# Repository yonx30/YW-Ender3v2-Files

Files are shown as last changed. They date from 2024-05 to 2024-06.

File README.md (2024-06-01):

# YW's Ender 3v2 Files
Repo for my custom files for the Ender 3v2 Enclosure and Jyers firmware.

## Modified Ender 3v2 



### Lack Enclosure
Printable parts to construct a standard I3 style 3D printer enclosure using 2x Ikea Lacks

Lack enclosure remixed based on the Ender 3 V2 Ikea Lack 3D Printer Enclosure design by User moomoo124578 - Link: https://www.thingiverse.com/thing:4873172

Uses 560mm x 465mm (22'' x 18.3'') 2mm thick acrylic panels for the sides, and 2x pieces of 280mm x 465mm (11'' x 18.3'') 3mm thick acrylic panels for the front doors. All other printed (eg. magnet holders, handles) and purchased parts (eg. screws, hinges) are used as originally uploaded by moomoo124578 as above.

Printable legs have internal holes that are meant to house embedded M3 Hexagonal Nuts, to help screw the front panel hinges to the enclosure. When slicing the upper and lower legs, the print should be paused at the relevant heights (depending on the layer height used) to allow insertion of the nuts vertically into the print. The print will then bridge over then inserted nuts and embed them. For the pictures below, a pause is inserted after Layer 279 is printed to slot the M3 nut into the highlighted hole.



### Motherboard Enclosure
Motherboard enclosure made using base dimensions from User GalvanicGlaze's enclosure - Link: https://www.thingiverse.com/thing:4742032\ 

Uses 3x pieces of 20mm x 10mm x 2mm neodynium magnets to hold the cover shut, and these 2x 1.5in door hinges (Link - https://www.aliexpress.us/item/2251832452494262.html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), along with 2x M3x8 screws and 2x M3 nuts.

### MiniMe Hotend Remix
Remixed User P_design's 5015 MiniMe model - Link: https://www.thingiverse.com/thing:4375296

Allows removal of the duct portion without needing to remove the hotend fan, providing easier access to the hotend (eg. for nozzle changes). Requires M3 hexagonal nuts to be embedded into duct after printing.

## Ender 3v2 Jyers Firmware
Uses Jyers Marlin firmware with modified parameters - Link: https://github.com/Jyers/Marlin/releases

Guide to compiling - Link: https://www.youtube.com/watch?v=so0FfFVEmiw

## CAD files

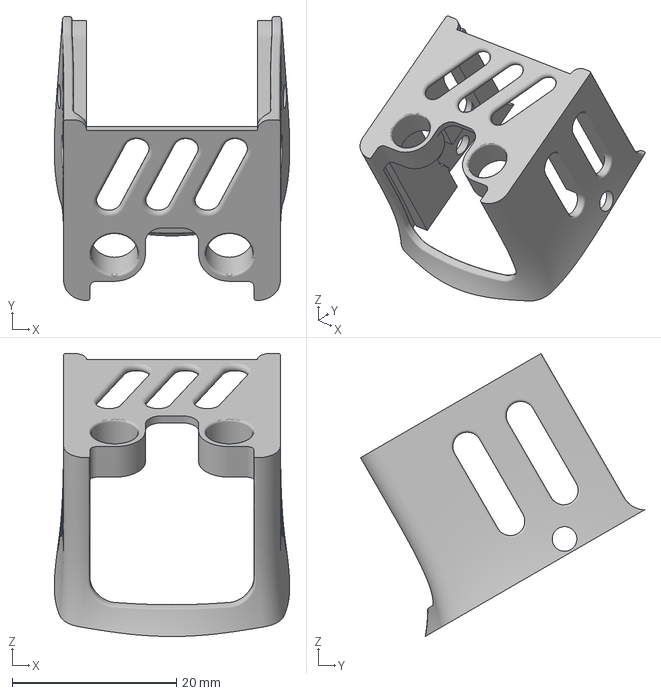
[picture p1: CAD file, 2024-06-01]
3MF CAD Files/MiniMe Remix Mount.3mf
28.7 x 34.6 x 34.5 mm

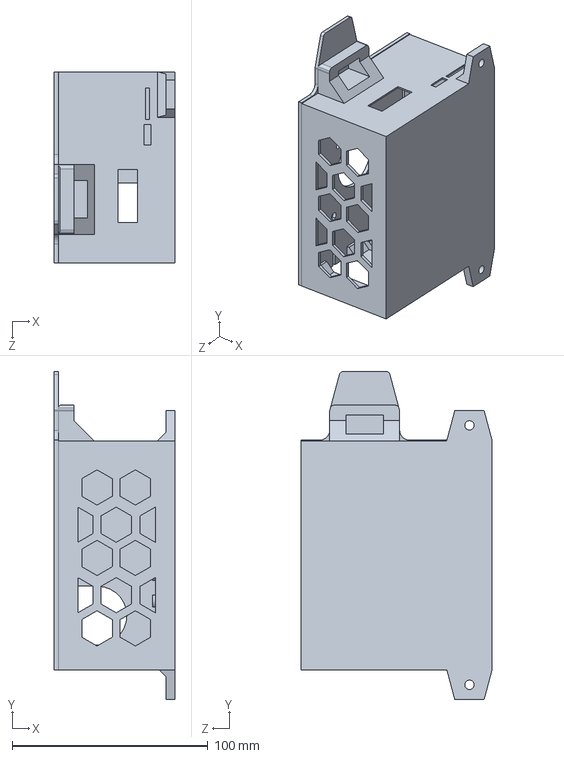
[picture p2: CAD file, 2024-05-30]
Solidworks Part Files/Ender 3v2 Board Enclosure v2.SLDPRT
61.6 x 167.4 x 97.5 mm

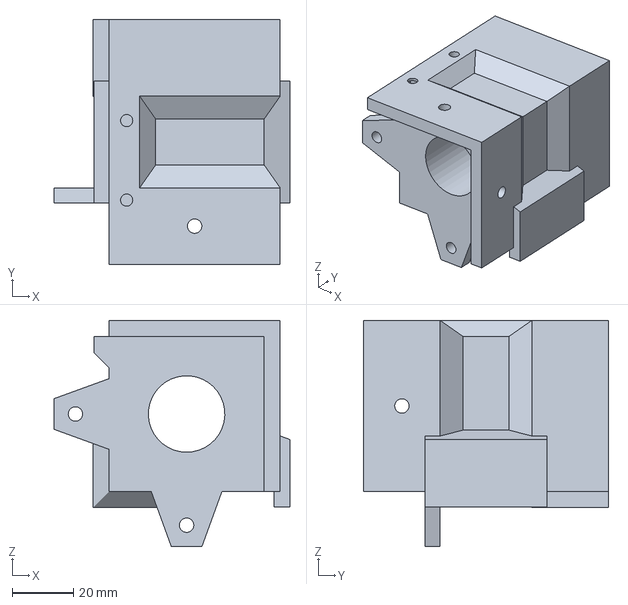
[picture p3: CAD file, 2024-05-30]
3MF CAD Files/Upper Leg Extension MkII-4.3mf
77.2 x 80.0 x 74.0 mm

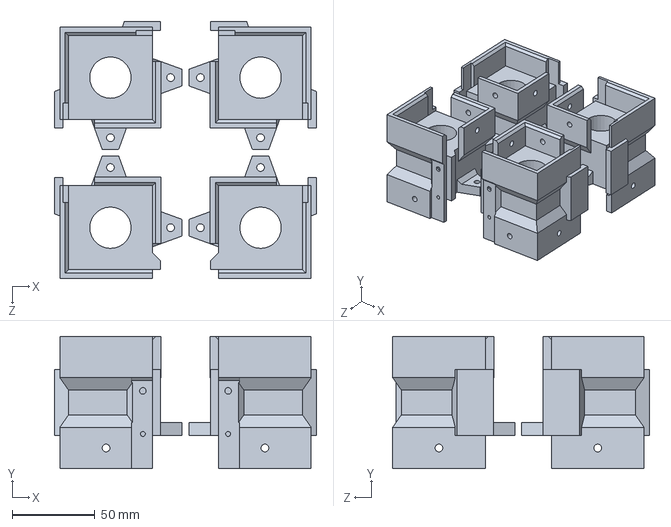
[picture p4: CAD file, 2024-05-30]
Solidworks Part Files/Upper Leg Extension MkIII.SLDPRT
158.3 x 80.0 x 155.1 mm

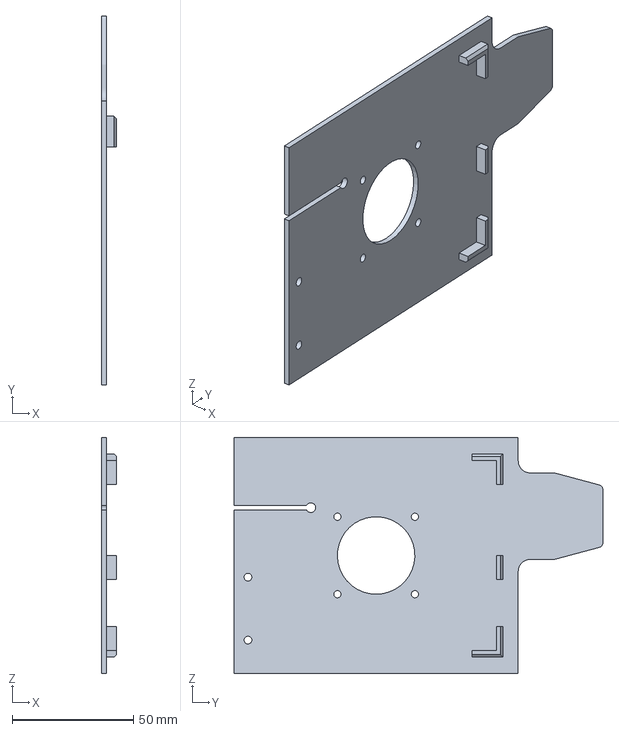
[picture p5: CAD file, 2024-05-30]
3MF CAD Files/Ender 3 V2 Motherboard Enclosure Cover.3MF
6.10 x 152.4 x 97.5 mm

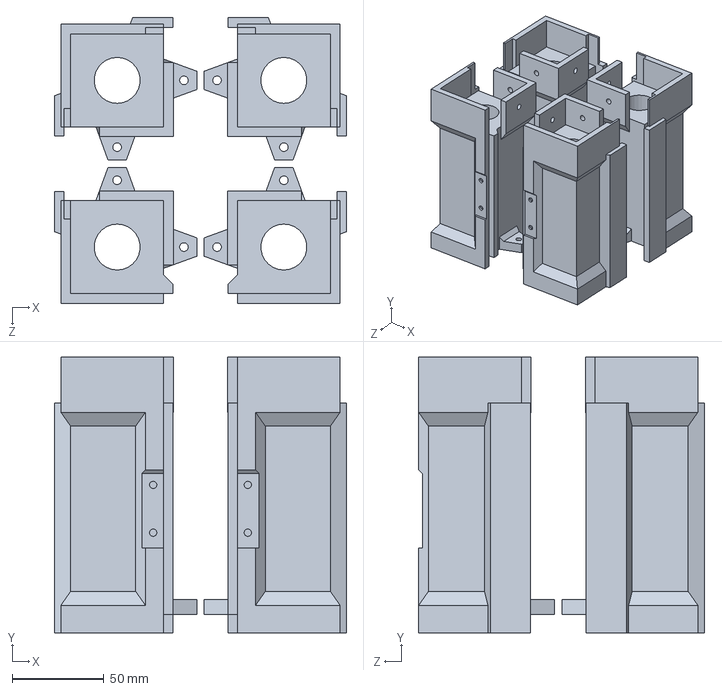
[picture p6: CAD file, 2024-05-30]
Solidworks Part Files/Lower Leg Extension MkIII.SLDPRT
158.9 x 150.0 x 155.4 mm

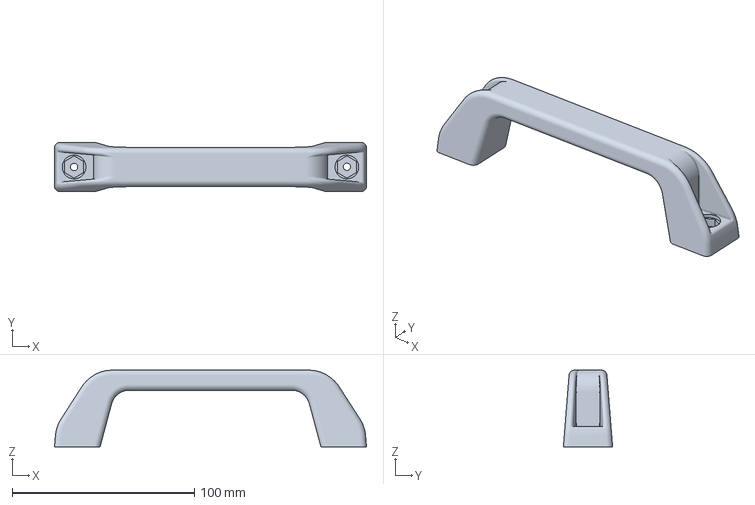
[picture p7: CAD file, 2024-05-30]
3MF CAD Files/Handle (through hole).3MF
171.0 x 27.0 x 42.0 mm

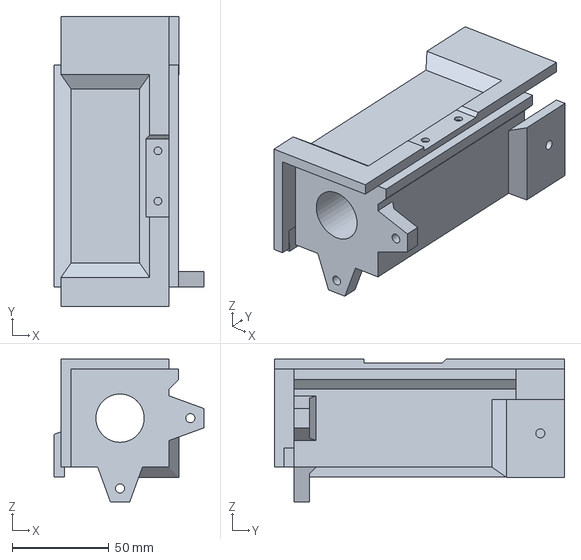
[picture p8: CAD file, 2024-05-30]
3MF CAD Files/Lower Leg Extension MkII-1.3MF
77.5 x 150.0 x 74.0 mm

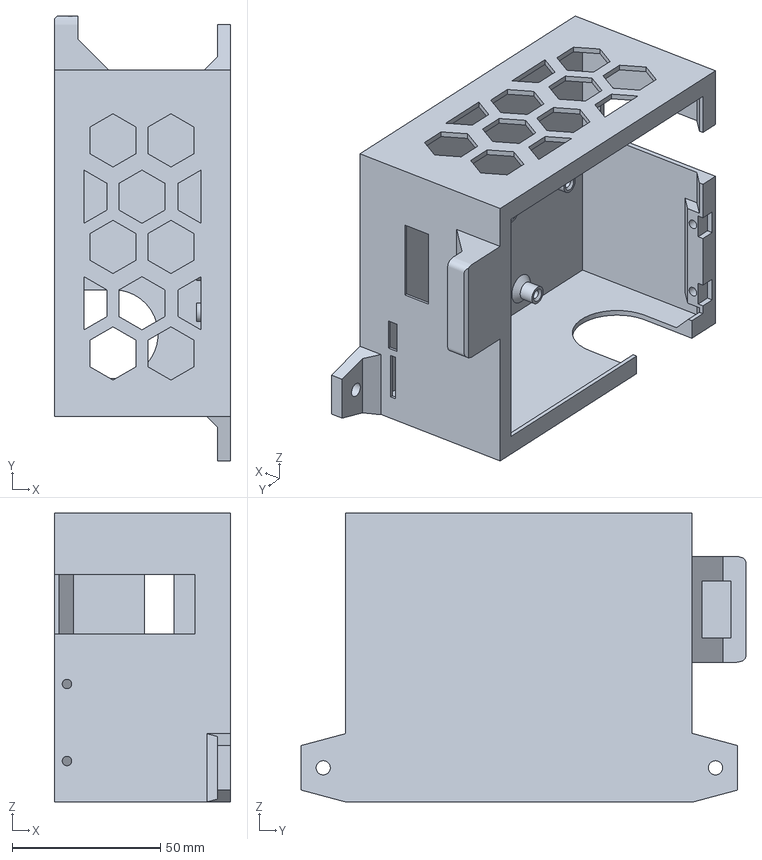
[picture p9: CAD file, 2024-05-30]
3MF CAD Files/Ender 3 V2 Motherboard Enclosure Body.3MF
59.5 x 150.2 x 97.5 mm

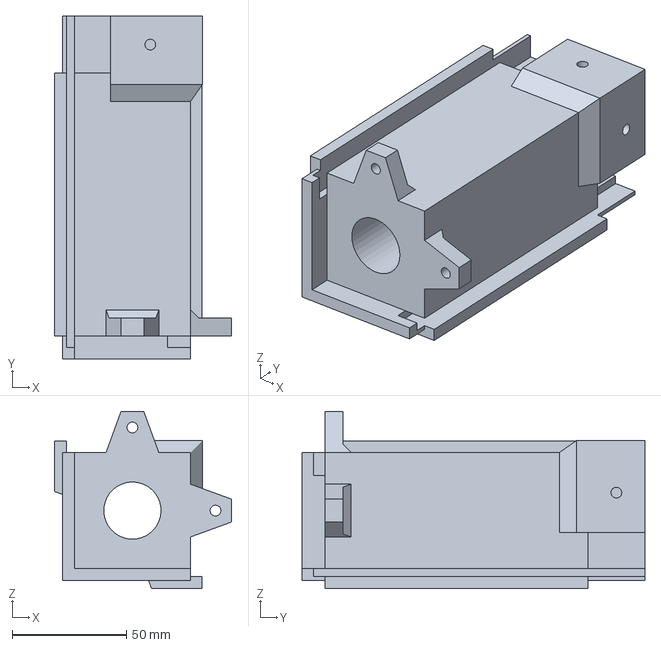
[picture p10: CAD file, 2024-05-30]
3MF CAD Files/Lower Leg Extension MkII-2.3MF
77.5 x 150.0 x 77.4 mm

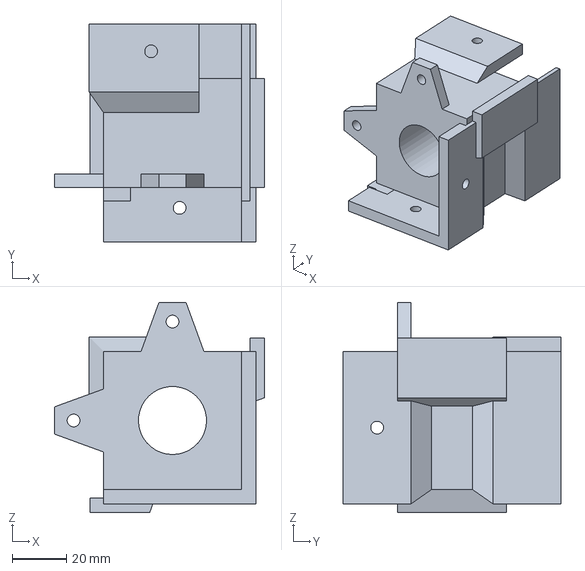
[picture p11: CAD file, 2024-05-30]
3MF CAD Files/Upper Leg Extension MkII-2.3mf
77.2 x 80.0 x 77.2 mm

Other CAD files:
3MF CAD Files/Upper Leg Extension MkII-3.3mf
3MF CAD Files/Lower Leg Extension MkII-3.3MF
3MF CAD Files/Lower Leg Extension MkII-4.3MF
3MF CAD Files/Upper Leg Extension MkII-1.3mf

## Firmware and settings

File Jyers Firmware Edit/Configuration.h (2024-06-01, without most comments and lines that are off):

#pragma once
#define CONFIGURATION_H_VERSION 02000902
#define STRING_CONFIG_H_AUTHOR "Jacob Myers" // Who made the changes.
#define SHOW_BOOTSCREEN
#define SERIAL_PORT 1
#define BAUDRATE 115200
  #define MOTHERBOARD BOARD_CREALITY_V4
#define CUSTOM_MACHINE_NAME "YW Ender-3 V2"
#if LINEAR_AXES >= 4
  #define AXIS4_NAME 'A' // :['A', 'B', 'C', 'U', 'V', 'W']
#endif
#if LINEAR_AXES >= 5
  #define AXIS5_NAME 'B' // :['A', 'B', 'C', 'U', 'V', 'W']
#endif
#if LINEAR_AXES >= 6
  #define AXIS6_NAME 'C' // :['A', 'B', 'C', 'U', 'V', 'W']
#endif
#define EXTRUDERS 1
#define DEFAULT_NOMINAL_FILAMENT_DIA 1.75
#define TEMP_SENSOR_0 1
#define TEMP_SENSOR_1 0
#define TEMP_SENSOR_2 0
#define TEMP_SENSOR_3 0
#define TEMP_SENSOR_4 0
#define TEMP_SENSOR_5 0
#define TEMP_SENSOR_6 0
#define TEMP_SENSOR_7 0
#define TEMP_SENSOR_BED 1
#define TEMP_SENSOR_PROBE 0
#define TEMP_SENSOR_CHAMBER 0
#define TEMP_SENSOR_COOLER 0
#define TEMP_SENSOR_BOARD 0
#define TEMP_SENSOR_REDUNDANT 0
#define DUMMY_THERMISTOR_998_VALUE  25
#define DUMMY_THERMISTOR_999_VALUE 100
#define TEMP_RESIDENCY_TIME         10  // (seconds) Time to wait for hotend to "settle" in M109
#define TEMP_WINDOW                  1  // (°C) Temperature proximity for the "temperature reached" timer
#define TEMP_HYSTERESIS              3  // (°C) Temperature proximity considered "close enough" to the target
#define TEMP_BED_RESIDENCY_TIME     10  // (seconds) Time to wait for bed to "settle" in M190
#define TEMP_BED_WINDOW              1  // (°C) Temperature proximity for the "temperature reached" timer
#define TEMP_BED_HYSTERESIS          3  // (°C) Temperature proximity considered "close enough" to the target
#define TEMP_CHAMBER_RESIDENCY_TIME 10  // (seconds) Time to wait for chamber to "settle" in M191
#define TEMP_CHAMBER_WINDOW          1  // (°C) Temperature proximity for the "temperature reached" timer
#define TEMP_CHAMBER_HYSTERESIS      3  // (°C) Temperature proximity considered "close enough" to the target
#if TEMP_SENSOR_REDUNDANT
  #define TEMP_SENSOR_REDUNDANT_SOURCE    E1  // The sensor that will provide the redundant reading.
  #define TEMP_SENSOR_REDUNDANT_TARGET    E0  // The sensor that we are providing a redundant reading for.
  #define TEMP_SENSOR_REDUNDANT_MAX_DIFF  10  // (°C) Temperature difference that will trigger a print abort.
#endif
#define HEATER_0_MINTEMP   0
#define HEATER_1_MINTEMP   5
#define HEATER_2_MINTEMP   5
#define HEATER_3_MINTEMP   5
#define HEATER_4_MINTEMP   5
#define HEATER_5_MINTEMP   5
#define HEATER_6_MINTEMP   5
#define HEATER_7_MINTEMP   5
#define BED_MINTEMP        0
#define CHAMBER_MINTEMP    5
#define HEATER_0_MAXTEMP 275
#define HEATER_1_MAXTEMP 275
#define HEATER_2_MAXTEMP 275
#define HEATER_3_MAXTEMP 275
#define HEATER_4_MAXTEMP 275
#define HEATER_5_MAXTEMP 275
#define HEATER_6_MAXTEMP 275
#define HEATER_7_MAXTEMP 275
#define BED_MAXTEMP      120
#define CHAMBER_MAXTEMP  60
#define HOTEND_OVERSHOOT 15   // (°C) Forbid temperatures over MAXTEMP - OVERSHOOT
#define BED_OVERSHOOT    10   // (°C) Forbid temperatures over MAXTEMP - OVERSHOOT
#define COOLER_OVERSHOOT  2   // (°C) Forbid temperatures closer than OVERSHOOT
#define PIDTEMP
#define BANG_MAX 255     // Limits current to nozzle while in bang-bang mode; 255=full current
#define PID_MAX BANG_MAX // Limits current to nozzle while PID is active (see PID_FUNCTIONAL_RANGE below); 255=full current
#define PID_K1 0.95      // Smoothing factor within any PID loop
    #define DEFAULT_Kp  28.72
    #define DEFAULT_Ki   2.62
    #define DEFAULT_Kd  78.81
#define PIDTEMPBED
#define MAX_BED_POWER 255 // limits duty cycle to bed; 255=full current
  #define DEFAULT_bedKp 462.10
  #define DEFAULT_bedKi  85.47
  #define DEFAULT_bedKd 624.59
#define MAX_CHAMBER_POWER 255 // limits duty cycle to chamber heater; 255=full current
  #define PID_FUNCTIONAL_RANGE 10 // If the temperature difference between the target temperature and the actual temperature
#define PREVENT_COLD_EXTRUSION
#define EXTRUDE_MINTEMP 160
#define PREVENT_LENGTHY_EXTRUDE
#define EXTRUDE_MAXLENGTH 1000
#define THERMAL_PROTECTION_HOTENDS // Enable thermal protection for all extruders
#define THERMAL_PROTECTION_BED     // Enable thermal protection for the heated bed
#define THERMAL_PROTECTION_COOLER  // Enable thermal protection for the laser cooling
#define USE_XMIN_PLUG
#define USE_YMIN_PLUG
#define USE_ZMIN_PLUG
#define ENDSTOPPULLUPS
#define X_MIN_ENDSTOP_INVERTING false // Set to true to invert the logic of the endstop.
#define Y_MIN_ENDSTOP_INVERTING false // Set to true to invert the logic of the endstop.
#define Z_MIN_ENDSTOP_INVERTING false // Set to true to invert the logic of the endstop.
#define I_MIN_ENDSTOP_INVERTING false // Set to true to invert the logic of the endstop.
#define J_MIN_ENDSTOP_INVERTING false // Set to true to invert the logic of the endstop.
#define K_MIN_ENDSTOP_INVERTING false // Set to true to invert the logic of the endstop.
#define X_MAX_ENDSTOP_INVERTING false // Set to true to invert the logic of the endstop.
#define Y_MAX_ENDSTOP_INVERTING false // Set to true to invert the logic of the endstop.
#define Z_MAX_ENDSTOP_INVERTING false // Set to true to invert the logic of the endstop.
#define I_MAX_ENDSTOP_INVERTING false // Set to true to invert the logic of the endstop.
#define J_MAX_ENDSTOP_INVERTING false // Set to true to invert the logic of the endstop.
#define K_MAX_ENDSTOP_INVERTING false // Set to true to invert the logic of the endstop.
#define Z_MIN_PROBE_ENDSTOP_INVERTING false // Set to true to invert the logic of the probe.
#define X_DRIVER_TYPE TMC2208_STANDALONE
#define Y_DRIVER_TYPE TMC2208_STANDALONE
#define Z_DRIVER_TYPE TMC2208_STANDALONE
#define E0_DRIVER_TYPE TMC2208_STANDALONE
#define ENDSTOP_INTERRUPTS_FEATURE
#define DEFAULT_AXIS_STEPS_PER_UNIT   { 79.7, 80.0, 409.8, 714.5 } // Actual default is { 80, 80, 400, 93 }, this is my own calibrateed one
#define DEFAULT_MAX_FEEDRATE          { 500, 500, 5, 25 }
#define DEFAULT_MAX_ACCELERATION      { 1000, 1000, 200, 1500 }
#define DEFAULT_ACCELERATION          750    // X, Y, Z and E acceleration for printing moves
#define DEFAULT_RETRACT_ACCELERATION  500    // E acceleration for retracts
#define DEFAULT_TRAVEL_ACCELERATION   1000    // X, Y, Z acceleration for travel (non printing) moves
#define CLASSIC_JERK
  #define DEFAULT_XJERK 10.0
  #define DEFAULT_YJERK 10.0
  #define DEFAULT_ZJERK  0.3
#define DEFAULT_EJERK    5.0  // May be used by Linear Advance
#define S_CURVE_ACCELERATION
#define USE_PROBE_FOR_Z_HOMING
#define BLTOUCH
#define NOZZLE_TO_PROBE_OFFSET { -44, -7, 0 }
#define PROBING_MARGIN 20
#define XY_PROBE_FEEDRATE (133*60)
#define Z_PROBE_FEEDRATE_FAST (3*75)
#define Z_PROBE_FEEDRATE_SLOW (Z_PROBE_FEEDRATE_FAST / 3)
#define MULTIPLE_PROBING 2
#define Z_CLEARANCE_DEPLOY_PROBE   9 // Z Clearance for Deploy/Stow
#define Z_CLEARANCE_BETWEEN_PROBES  1 // Z Clearance between probe points
#define Z_CLEARANCE_MULTI_PROBE     1 // Z Clearance between multiple probes
#define Z_PROBE_LOW_POINT          -2 // Farthest distance below the trigger-point to go before stopping
#define Z_PROBE_OFFSET_RANGE_MIN -10
#define Z_PROBE_OFFSET_RANGE_MAX 10
#define Z_MIN_PROBE_REPEATABILITY_TEST
#define X_ENABLE_ON 0
#define Y_ENABLE_ON 0
#define Z_ENABLE_ON 0
#define E_ENABLE_ON 0 // For all extruders
#define DISABLE_X false
#define DISABLE_Y false
#define DISABLE_Z false
#define DISABLE_E false             // Disable the extruder when not stepping
#define DISABLE_INACTIVE_EXTRUDER   // Keep only the active extruder enabled
#define INVERT_X_DIR false
#define INVERT_Y_DIR false
#define INVERT_Z_DIR true
#define INVERT_E0_DIR false
#define INVERT_E1_DIR false
#define INVERT_E2_DIR false
#define INVERT_E3_DIR false
#define INVERT_E4_DIR false
#define INVERT_E5_DIR false
#define INVERT_E6_DIR false
#define INVERT_E7_DIR false
#define HOME_AFTER_DEACTIVATE   // Require rehoming after steppers are deactivated. Also enable NO_MOTION_BEFORE_HOMING for extra safety.
#define X_HOME_DIR -1
#define Y_HOME_DIR -1
#define Z_HOME_DIR -1
#define X_BED_SIZE 225
#define Y_BED_SIZE 225
#define X_MIN_POS 0
#define Y_MIN_POS 0
#define Z_MIN_POS 0
#define X_MAX_POS X_BED_SIZE + 15 // Extended max to allow the probe to reach more of the bed.
#define Y_MAX_POS Y_BED_SIZE
#define Z_MAX_POS 245
#define MIN_SOFTWARE_ENDSTOPS
  #define MIN_SOFTWARE_ENDSTOP_X
  #define MIN_SOFTWARE_ENDSTOP_Y
  #define MIN_SOFTWARE_ENDSTOP_Z
  #define MIN_SOFTWARE_ENDSTOP_I
  #define MIN_SOFTWARE_ENDSTOP_J
  #define MIN_SOFTWARE_ENDSTOP_K
#define MAX_SOFTWARE_ENDSTOPS
  #define MAX_SOFTWARE_ENDSTOP_X
  #define MAX_SOFTWARE_ENDSTOP_Y
  #define MAX_SOFTWARE_ENDSTOP_Z
  #define MAX_SOFTWARE_ENDSTOP_I
  #define MAX_SOFTWARE_ENDSTOP_J
  #define MAX_SOFTWARE_ENDSTOP_K
#define FILAMENT_RUNOUT_SENSOR
  #define FIL_RUNOUT_ENABLED_DEFAULT false // Enable the sensor on startup. Override with M412 followed by M500.
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

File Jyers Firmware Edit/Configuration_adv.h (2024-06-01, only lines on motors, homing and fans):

#define E0_AUTO_FAN_PIN -1
#define E1_AUTO_FAN_PIN -1
#define E2_AUTO_FAN_PIN -1
#define E3_AUTO_FAN_PIN -1
#define E4_AUTO_FAN_PIN -1
#define E5_AUTO_FAN_PIN -1
#define E6_AUTO_FAN_PIN -1
#define E7_AUTO_FAN_PIN -1
#define CHAMBER_AUTO_FAN_PIN -1
#define COOLER_AUTO_FAN_PIN -1
#define COOLER_FAN_PIN -1
#define HOMING_BUMP_MM      { 5, 5, 2 }       // (mm) Backoff from endstops after first bump
#define HOMING_BUMP_DIVISOR { 6, 6, 4 }       // Re-Bump Speed Divisor (Divides the Homing Feedrate)
#define QUICK_HOME                            // If G28 contains XY do a diagonal move first
#define MICROSTEP_MODES { 16, 16, 16, 16, 16, 16 } // [1,2,4,8,16]
#define ADVANCED_PAUSE_FEATURE
  #define ADVANCED_PAUSE_PURGE_FEEDRATE        3  // (mm/s) Extrude feedrate (after loading). Should be slower than load feedrate.
  #define ADVANCED_PAUSE_PURGE_LENGTH         50  // (mm) Length to extrude after loading.
  #define ADVANCED_PAUSE_RESUME_PRIME          0  // (mm) Extra distance to prime nozzle after returning from park.

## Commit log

2024-06-01 Rename Ender 3 V2 - Enclosure Body.3MF to Ender 3 V2 Motherboard Enclosure Body.3MF
    [Ender 3 V2 Motherboard Enclosure Body.3MF]
2024-06-01 Rename Ender 3 V2 - Enclosure Cover.3MF to Ender 3 V2 Motherboard Enclosure Cover.3MF
    [Ender 3 V2 Motherboard Enclosure Cover.3MF]

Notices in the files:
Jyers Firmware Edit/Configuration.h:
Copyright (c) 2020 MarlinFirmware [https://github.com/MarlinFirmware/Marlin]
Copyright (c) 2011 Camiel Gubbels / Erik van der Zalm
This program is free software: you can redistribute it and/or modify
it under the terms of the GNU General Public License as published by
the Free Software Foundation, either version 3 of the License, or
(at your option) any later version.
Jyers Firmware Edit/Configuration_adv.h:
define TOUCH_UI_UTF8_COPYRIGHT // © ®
